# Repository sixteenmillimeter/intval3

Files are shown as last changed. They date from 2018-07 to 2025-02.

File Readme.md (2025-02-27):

# INTVAL3

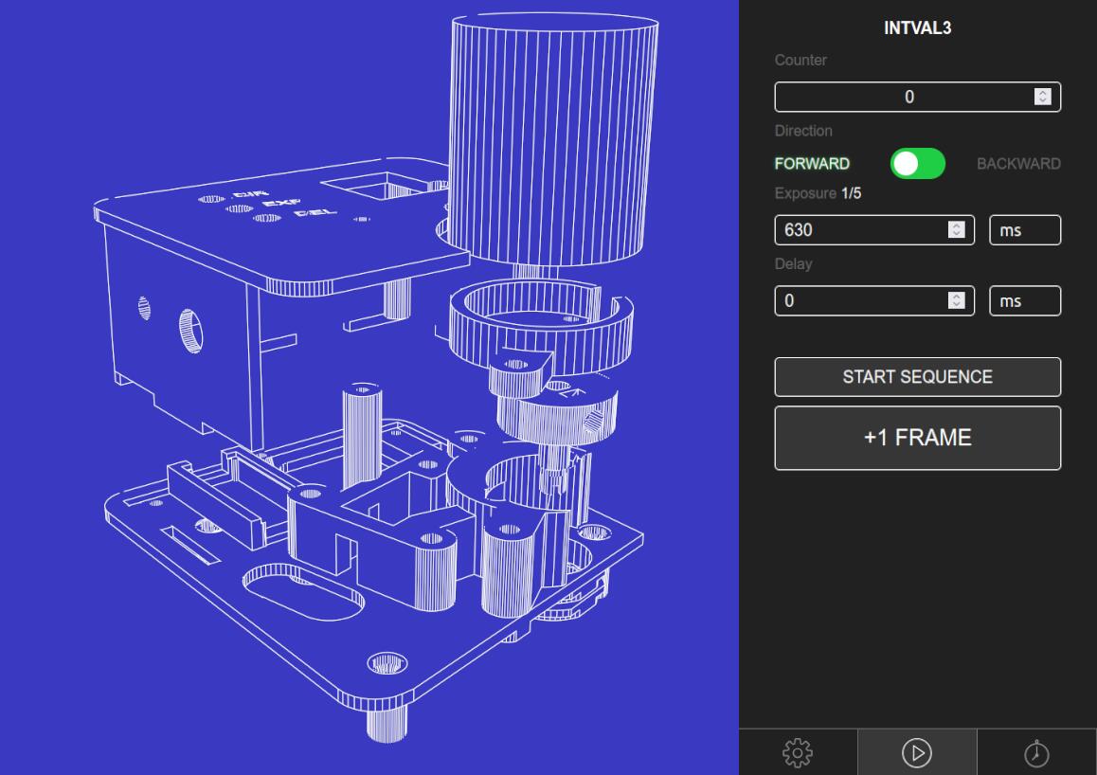
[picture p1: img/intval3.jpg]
intval3 wireframe rendering next to mobile app UI


### [Project Home - git.sixteenmillimeter.com/16mm/intval3](https://git.sixteenmillimeter.com/16mm/intval3)

* Github Mirror - [github.com/sixteenmillimeter/intval3](https://github.com/sixteenmillimeter/intval3)
* Gitlab Mirror - [gitlab.com/16mm/intval3](https://gitlab.com/16mm/intval3)

### What is this?

INTVAL3 is an open source intervalometer for the Bolex 16mm camera. The goal of the project is to create a cheap-to-make intervalometer that can be used to automate time-lapse or animation on the Bolex using mobile, web or physical controls.

This is the third incarnation of the INTVAL project, this time utilizing the [Raspberry Pi Zero W](https://www.raspberrypi.org/products/raspberry-pi-zero-w/) for Wifi and Bluetooth control. Earlier versions, the [INTVAL](https://github.com/sixteenmillimeter/INTVAL) and [INTVAL2](https://github.com/sixteenmillimeter/intval2) were Arduino-based. The original INTVAL used a solenoid (!!!) to hammer a camera release cable, while the second attempt was a proving ground for the motor-and-key hardware used in this version. 

The [INTVAL2](https://github.com/sixteenmillimeter/intval2) project should be used if you prefer a simpler, physical interface approach.

Does your browser support [Web Bluetooth](https://caniuse.com/#feat=web-bluetooth)? Control your INTVAL3 using this web app.

### [intval.sixteenmillimeter.com](https://intval.sixteenmillimeter.com)

### Components

* [Firmware](#firmware) for the Raspberry Pi Zero W running [Node.js](https://nodejs.org) on Raspian
* [Mobile app](#mobile) for controlling device using [Cordova](https://cordova.apache.org/) + [Bleno](https://github.com/sandeepmistry/bleno)
* [Web app](#web) for controlling device using [Restify](http://restify.com/)
* Hardware files, parts models for 3D printing, laser cutting and CNC
* PCB design for a Raspberry Pi Zero W Bonnet
* [Parts list](#parts-list)

## Firmware

The firmware of the INTVAL3 is a node.js application running on the Raspian OS intended for installation on the Raspberry Pi Zero W. 

## Mobile App

The INTVAL3 mobile app controls the intervalometer over Bluetooth. It can be used to configure the settings on the intervalometer such as exposure length, delay between frames and the direction of the film. The app can also be used to trigger individual frames, as well as start and stop sequences. As an experimental feature, film exposure settings can be determined with the camera on a mobile device.

## Web App

As a function of the firmware, there is an embedded web application that is hosted on the INTVAL3. When connected to a wifi network (via the mobile app) users are able to control the intervalometer from a browser. Users are also able to trigger functions and change settings on the intervalometer firmware from the command line by using cURL or wget, so actions can be scripted and automated from an external machine.

## Hardware

All of the non-electronic hardware is generated from OpenSCAD scripts and built into either STL files for 3D printing or DXF files for laser cutting or CNCing.

Electronics designs are available in the form of a Fritzing file, Gerber files, a wiring diagram and a mask image that can be used to fabricate a board from a blank PCB.

Prototype of the bare PCB of the "bonnet" for the Raspberry Pi Zero W are available for order from OSH Park. See the parts list below of components for this board.



<br />

## Parts

1. Raspberry Pi Zero W - [[Adafruit](https://www.adafruit.com/product/3400)] [[Sparkfun](https://www.sparkfun.com/products/14277)] [[Amazon](https://amzn.to/2Wf46J8)]
2. L298N Breakout Board - [[BC Robotics](https://www.bc-robotics.com/shop/l298n-motor-driver-board/)] [[Amazon](https://amzn.to/35CRFKa)]
3. 120RPM 12VDC Motor - [[Amazon](https://amzn.to/2YDGFe2)]
4. Microswitch w/ Roller - [[Adafruit](https://www.adafruit.com/product/819)] [[Amazon](https://amzn.to/2YDGFe2)]
5. L7805 5V Regulator - [[Adafruit](https://www.adafruit.com/product/2164)] [Sparkfun](https://www.sparkfun.com/products/107)] [[Amazon](https://amzn.to/2WaF39O)]
6. 2x Thru-hole Resistors - 330 Ohm
7. 1x Thru-hole Capacitor - 10 uF
8. 1x Thru-hole Capacitor - 100 uF
9. 4x Terminal blocks
10. 1x 3.5mm Socket Audio Connector - [[Amazon](https://amzn.to/2SGFVAY)]
11. 1x 3.5mm Stereo Audio Cable - [[Amazon](https://amzn.to/3beNPrQ)]
12. 1x Momentary Push Button 7mm Diameter - [[Amazon](https://amzn.to/2LavqBK)]
13. 1x Micro Switch w/ Roller Lever 28mm x 30.2mm x 10.2mm - [[Adafruit](https://www.adafruit.com/products/819)] [[Amazon](https://amzn.to/2SMBFzX)]
14. 1x Skateboard bearing 608-2RS - [[Amazon](https://amzn.to/3b7X2lC)]
15. 4x M3.5 - 0.6 x 20mm Screws
16. 3x M2 - 0.6 x 15mm Bolts
17. 6x M5 - 0.8 x 25mm Bolts
18. 4x M5 - 0.8 Nuts

* (Optional) Proto Bonnet - [[Adafruit](https://www.adafruit.com/product/3203)]
* (Optional) INTVAL3 Bonnet - [[OSH Park](https://oshpark.com/shared_projects/SkPyOK5S)]

## License
MIT License

Copyright (c) 2020 Matt McWilliams

Permission is hereby granted, free of charge, to any person obtaining a copy
of this software and associated documentation files (the "Software"), to deal
in the Software without restriction, including without limitation the rights
to use, copy, modify, merge, publish, distribute, sublicense, and/or sell
copies of the Software, and to permit persons to whom the Software is
furnished to do so, subject to the following conditions:

The above copyright notice and this permission notice shall be included in all
copies or substantial portions of the Software.

THE SOFTWARE IS PROVIDED "AS IS", WITHOUT WARRANTY OF ANY KIND, EXPRESS OR
IMPLIED, INCLUDING BUT NOT LIMITED TO THE WARRANTIES OF MERCHANTABILITY,
FITNESS FOR A PARTICULAR PURPOSE AND NONINFRINGEMENT. IN NO EVENT SHALL THE
AUTHORS OR COPYRIGHT HOLDERS BE LIABLE FOR ANY CLAIM, DAMAGES OR OTHER
LIABILITY, WHETHER IN AN ACTION OF CONTRACT, TORT OR OTHERWISE, ARISING FROM,
OUT OF OR IN CONNECTION WITH THE SOFTWARE OR THE USE OR OTHER DEALINGS IN THE
SOFTWARE.

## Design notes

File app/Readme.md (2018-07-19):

# INTVAL3

## Mobile App

The INTVAL3 mobile app is built using the Cordova framework for cross-platform deployment to iOS and Android.

## Requirements

* node.js
* npm
* Cordova
* XCode (for iOS) and/or
* Android Studio (for Android)

## Installation

All of the required plugins can be installed directly by executing the `install.sh` script on a system which supports bash. This script will use the `cordova` application to install the Cordova plugins. Cordova also supports the npm package.json format, so plugins may be alternately installed simply by running a `npm install` command from within the `app` directory.

## Building

Once all dependencies and plugins are installed, you can build the INTVAL3 app by running

```cordova build ios```

or

```cordova build android```

This generates the application source code in the `platforms` directory, under either the `ios` or `android` directory depending on your build target. The app can be built and run on your device by going to the project file and opening it in your IDE, either XCode or Android Studio. Alternately it can be run on your device using the `cordova run ios` or `cordova run android` commands.

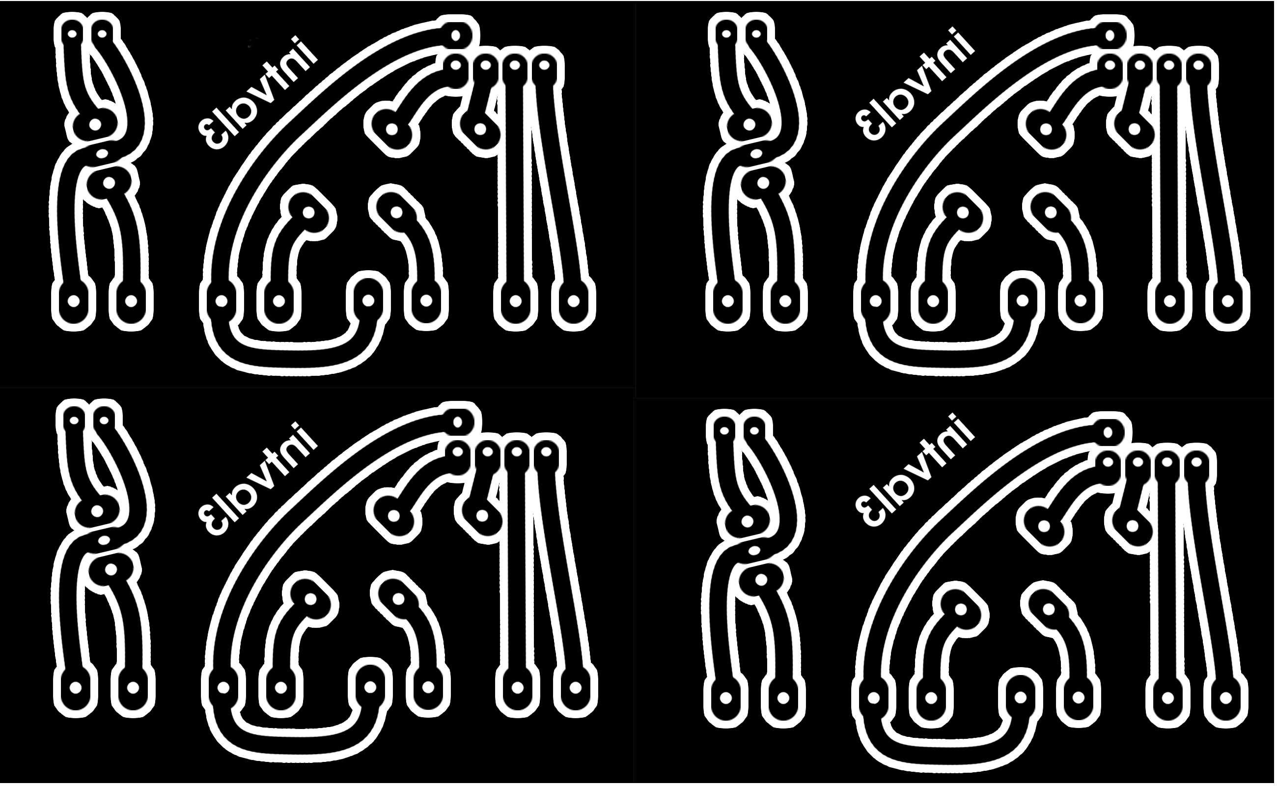
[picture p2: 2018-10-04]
hardware/intval3_0_prototype_mask_4_4x.png

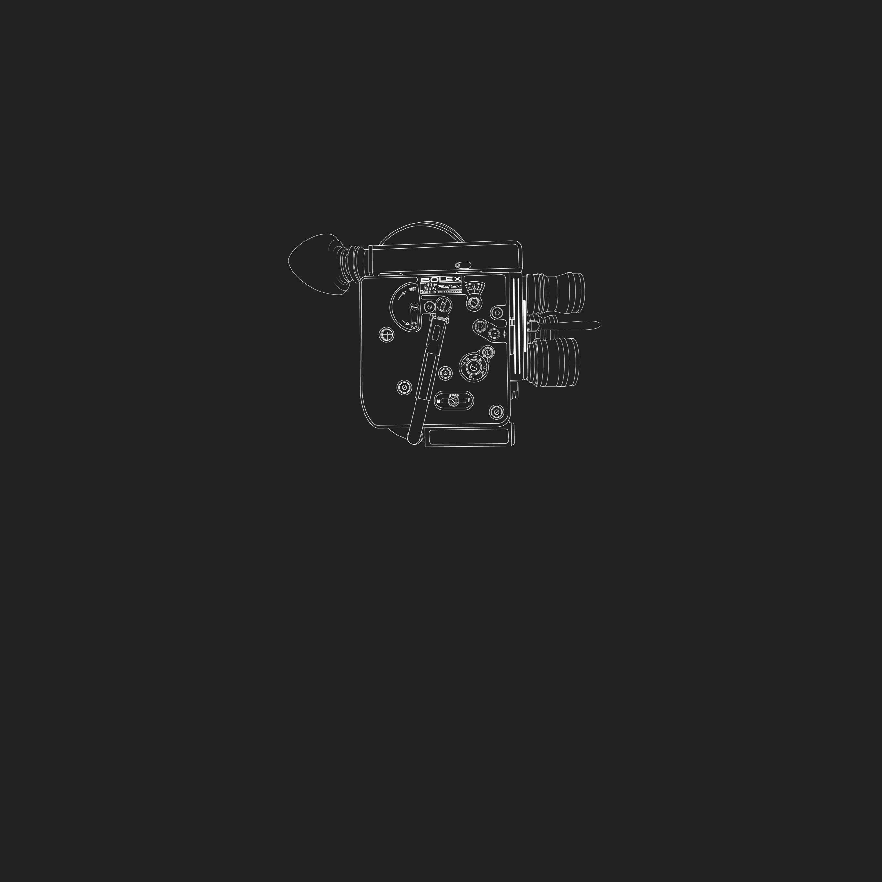
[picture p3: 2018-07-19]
app/res/screen/ios/Default@2x~universal~anyany.png

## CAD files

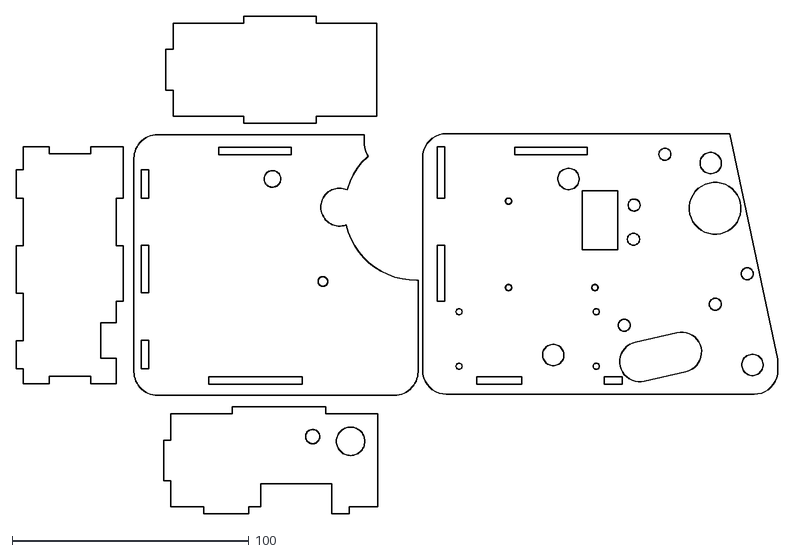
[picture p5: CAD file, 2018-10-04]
hardware/dxf/intval3_case.dxf
321.7 x 210.2

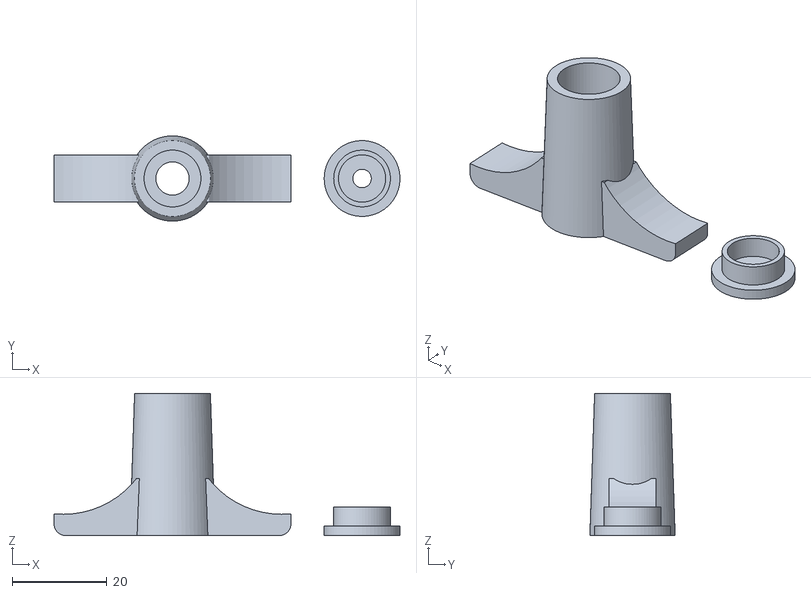
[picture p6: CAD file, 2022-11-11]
hardware/stl/intval3_plunger_plate.stl
73.0 x 18.0 x 30.0

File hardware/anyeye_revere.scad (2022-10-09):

module motor_set_screw_120 () {
    cube([10.19, 2.95, 2.95], center = true);
    translate([(10.19 / 2) - (2.56 / 2), 0, 0]) cube([2.56, 5.8, 5.8], center = true);    
}

module motor_set_screw_120_alt () {
    $fn = 60;
    cylinder(r = 2.95 / 2, h = 10.19, center= true);
    translate([0, 0, (10.19 / 2) - (2.56 / 2)]) cylinder(r = 5.8 / 2, h = 2.56, center = true);
}

module hobbled_rod_120 (h = 10) {
            d = 4.00;
        diff = 3.33;
    difference () {
        
        cylinder(r = d/2, h = h, center = true, $fn = 60);
        translate([d/2 + ((d/2) - (d - diff)), 0, 0]) cube([d, d, h + 1], center = true);
    }
}

module bearing_laser (x = 0, y = 0, z = 0, width= 8, hole = true) {
	innerD = 8.05;
	outerD = 22.1 - .4;
	fuzz = 0.1;
	translate ([x, y, z]) {
		difference () {
			cylinder(r = outerD / 2 + fuzz, h = width, center = true);
			if (hole) {
				cylinder(r = innerD / 2 - fuzz, h = width, center = true);
			}
		}
	}
}

/**
 *	Notched
 **/
module motor_key_120 (half = false, DECOYS = false, sides = 1, ALT = false) {
    
	outer_d = 27.5 + 2;
	notch_d = 10;
	height = 7 + 5 + 4;
	diff = 14 + 2.5 + 2;
    $fn = 60;
	difference () {
		union () {
			translate([0, 0, 12.1]) cylinder(r1 = 12 / 2, r2 = 12/2 + 4, h = 5, center = true);// padding against bearing
			translate([0, 0, diff + 1]) cylinder(r=outer_d/2, h= height -2, center= true, $fn=200); //large cylinder
			
		}
        //1 notch
		translate([0, 0, diff]) {
			translate ([-outer_d/2 - 2.5, 0, 0]) cylinder(r=notch_d/2, h= height, center= true); //notch
		}
		translate([0, 0, diff]) {
			translate ([-outer_d/2  -.5, -3.5 , 0]) rotate([0, 0, 100]) cube([15, 5, height], center = true); // smooth notch
			translate ([-outer_d/2  -.5, 3.5, 0]) rotate([0, 0, -100]) cube([15, 5, height], center = true); // smooth notch
		}
        
        if (sides == 2) {
            //2 notch
            translate([0, 0, diff]) {
                translate ([outer_d/2 + 2.5, 0, 0]) cylinder(r=notch_d/2, h= height, center= true); //notch
            }
            translate([0, 0, diff]) {
                translate ([outer_d/2  +.5, -3.5, 0]) rotate([0, 0, -100]) cube([15, 5, height], center = true); // smooth notch
                translate ([outer_d/2  +.5, 3.5, 0]) rotate([0, 0, 100]) cube([15, 5, height], center = true); // smooth notch
            }
        }
        
		//slot for hobbled(?) end
        translate([0, 0, 17 + 2]) {
             translate([0, 0, 6.5]) hobbled_rod_120(12);
            translate([6.42 - .2, 0, 4.3 - 1]) rotate([0, 90, 0]) motor_set_screw_120_alt();
            translate([14, 0, 4.3 - 1]) rotate([0, 90, 0]) cylinder(r2 = 6 / 2, r1 = 5.8 / 2, h = 6, center = true); //extension
            
        }
		//square void for bottom piece
		translate([0, 0, 10.5]) motor_key_bottom();
		
		if (half) {
			translate([0 - 50 , 0, -50]) cube([100, 100, 200]);
		}
	}
	
}

module motor_key_bottom () {
	$fn = 120;
	BEARING_INNER_D = 7.85;
	INNER_D = 4.08;
	OUTER_D = 11.08;
	FUZZ = 0.1;
	SQ = sqrt(pow(BEARING_INNER_D, 2) / 2);//largest square
	cube([SQ, SQ, SQ], center = true);
	translate([0, 0, -5.5]) cylinder(r=BEARING_INNER_D/2, h= 9, center= true);
	translate([0, 0, -5.5 - 5]) cylinder(r1= (INNER_D / 2) - FUZZ, r2= (INNER_D / 2) + FUZZ, h= 9.25, center= true);
	translate([0, 0, -5.5 - 4 - 1 - 1]) color(0, 0, 0) difference() {
		cylinder(r=(OUTER_D + 3) / 2, h = 6, center= true);
		translate([0, 0, -1.5]) cylinder(r2=(OUTER_D / 2) - FUZZ, r1=(OUTER_D / 2) + FUZZ, h = 6, center= true);
		translate([0, 0, .5]) rotate([90, 0, 0]) cylinder(r = 1, h = 20, center = true);
		translate([0, 0, -1.5]) cube([2, 20, 4], center = true);
	}
}

module reference_projector_shaft () {
	INNER_DIAMETER = 4.08;
	OUTER_DIAMETER = 11.08;
	H = 7.37;
	WHEEL_DIAMETER = 54;
	WHEEL_H = 3;
	STANDOFF = 6; 
	FUZZ = 0.1;
	
	$fn = 120;
	translate([0, 0, -15 + H]) difference () {
		cylinder(r = OUTER_DIAMETER / 2, h = 30, center = true);
		cylinder(r = INNER_DIAMETER / 2, h = 30 + 1, center = true);
	}
	translate([0, 0, -1.5]) cylinder(r = WHEEL_DIAMETER / 2, h = WHEEL_H, center = true); 
	translate([0, 0, H + 1.5 + STANDOFF]) difference () {
		cube([60, 60, 3], center = true);
		bearing_laser(hole=false);
	}
}

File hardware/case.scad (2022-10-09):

include <./modules.scad>
include <./variables.scad>

module l289N_holes (r = 3/2 - .2) {
    $fn = 60;
    DISTANCE = 36.5;
    H = 50;
    translate([0, 0, 0]) cylinder(r = r, h = H * 5, center = true);
    translate([DISTANCE, 0, 0]) cylinder(r = r, h = H * 5, center = true);
    translate([DISTANCE, DISTANCE, 0]) cylinder(r = r, h = H * 5, center = true);
    translate([0, DISTANCE, 0]) cylinder(r = r, h = H * 5, center = true);
}

module l289N_hole_test () {
    $fn = 40;
    difference () {
        cube([140, 40, 3], center = true);
        cylinder(r = 3/2, h = 50, center = true);
        translate([7, 0, 0]) cylinder(r = 3/2, h = 50, center = true);
        translate([7 * 2, 0, 0]) cylinder(r = 3/2 - .1, h = 50, center = true);
        translate([7 * 3, 0, 0]) cylinder(r = 3/2 - .2, h = 50, center = true);
        translate([7 * 4, 0, 0]) cylinder(r = 3/2 - .3, h = 50, center = true);
    }
}

module intval_panel_laser () {
    $fn = 40;
	difference () {
		union () {
			difference () {
				translate ([0, 0, 8.5]) {
					union () {
						translate([12 - 10, 0]) {
                            rotate([0, 0, -13]) {
                                rounded_cube([panel_2_x + 20 + 20, panel_2_y, 25.4/8], d = 20, center = true);
                            }
                        }
						//reinforces
						//translate([54, -12, -3]) rotate([0, 0, 89]) rounded_cube([110, 20, 4], 20, center = true);
						//translate([-17, 2, -3]) rotate([0, 0, 72]) rounded_cube([94, 13, 4], 13, center = true);
					}
				}
				for (i = [0 : len(xArray) - 1]) {
					bolex_pin_inner_laser(xArray[i], yArray[i]);
				}
			}
			//onetoone(26, 10, 4.5);
			//extends for onetoone
			

		}
		//onetoone(9, 14, 8.5);
		bearing_laser(54.5, 12, 6, width= 18, hole=false);
        translate([-38, -1, 0]) rotate([0, 0, -13]) l289N_holes();
        //translate ([6, -9, height + 3.5]) cylinder(r = bolt_inner, h = 50, center = true); //cover standoff hole
		//frame_counter_access(); //use the space
		m_p_access();
		remove_front();
		translate([6, 18, 0]) rotate([0, 0, -13]) cube([15, 25, 40], center=true); //motor wind key hole

		for (i = [0 : len(mm_x) - 1]) {
			translate([mm_x[i], mm_y[i], 0]) cylinder(r = bolt_inner, h = 100, center = true);
		}
        translate([0, 0, .25]) intval_laser_panel_cover();
            translate([-35, -24, 15]) rotate([0, 0, -13]) {
            translate([58 / 2, 23 / 2, 0]) cylinder(r = 3/2 - .2, h = 30, center = true, $fn = 20);
            translate([-58 / 2, 23 / 2, 0]) cylinder(r = 3/2 - .2, h = 30, center = true, $fn = 20);
            translate([58 / 2, -23 / 2, 0]) cylinder(r = 3/2 - .2, h = 30, center = true, $fn = 20);
            translate([-58 / 2, -23 / 2, 0]) cylinder(r = 3/2 - .2, h = 30, center = true, $fn = 20);
        }
	}

}

module intval_panel_laser_debug () {
    $fn = 40;
	difference () {
		union () {
			difference () {
				translate ([0, 0, 8.5]) {
					union () {
						translate([12 - 32.5, -5 + 9, 0]) {
                            rotate([0, 0, -13]) {
                                rounded_cube([panel_2_x + 20 + 65, panel_2_y, 25.4/8], d = 20, center = true);
                            }
                        }
						//reinforces
						//translate([54, -12, -3]) rotate([0, 0, 89]) rounded_cube([110, 20, 4], 20, center = true);
						//translate([-17, 2, -3]) rotate([0, 0, 72]) rounded_cube([94, 13, 4], 13, center = true);
					}
				}
				for (i = [0 : len(xArray) - 1]) {
					bolex_pin_inner_laser(xArray[i], yArray[i]);
				}
			}
			//onetoone(26, 10, 4.5);
			//extends for onetoone
			

		}
		//onetoone(9, 14, 8.5);
		bearing_laser(54.5, 12, 6, width= 18, hole=false);
        translate([-38, -1, 0]) rotate([0, 0, -13]) l289N_holes();
        //translate ([6, -9, height + 3.5]) cylinder(r = bolt_inner, h = 50, center = true); //cover standoff hole
		//frame_counter_access(); //use the space
		m_p_access();
		remove_front();
		translate([6, 18, 0]) rotate([0, 0, -13]) cube([15, 25, 40], center=true); //motor wind key hole

		for (i = [0 : len(mm_x) - 1]) {
			translate([mm_x[i], mm_y[i], 0]) cylinder(r = bolt_inner, h = 100, center = true);
		}
        intval_laser_panel_cover(DEBUG = true);
        translate ([4, 12, 0]) {
            translate([-51.5, -8.5, 0]) cylinder(r = 2.8/2, h = 100, center = true);
            translate([-51.5 - 66, -8.5 + 15, 0]) cylinder(r = 2.8/2, h = 100, center = true);
            translate([-51.5 + 11.5, -8 + 49, 0]) cylinder(r = 2.8/2, h = 100, center = true);
            translate([-51.5 - 54.5, -8.5 + 49 + 16, 0]) cylinder(r = 2.8/2, h = 100, center = true);
        }
	}
}

module bolex_pin_laser (x, y) {
	in = innerD;
    $fn = 120;
	translate ([x, y, 1]) {
		difference () {
			union () {
				translate([0, 0, (height / 2) - 3]) cylinder(r = (outerD + 5) / 2, h = 2, center = true);
				translate([0, 0, 1.175/2]) cylinder(r = outerD / 2, h = height + 1.175 , center = true);
			}
			cylinder(r = in / 2, h = height * 2, center = true);
			translate([0, 0, (height / 2) - 1.9]) cylinder(r1 =4.5 / 2, r2 = 6.7 / 2, h = 2, center = true);
            translate([0, 0, (height / 2) + 1]) cylinder(r = 6.7 / 2, h = 4, center = true);
		}
	}
}

module bolex_pin_laser_alt (x, y) {
    in = innerD;
    $fn = 120;
    translate ([x, y, 1]) {
        difference () {
            union () {
                translate([0, 0, (height / 2) + 1.5]) cylinder(r = (outerD + 1.5) / 2, h = 2, center = true);
                translate([0, 0, 1.175/2]) cylinder(r = outerD / 2, h = height + 1.175 - 1 , center = true);
            }
            cylinder(r = in / 2, h = height * 2, center = true);
            translate([0, 0, (height / 2) - 1.9]) cylinder(r1 =4.5 / 2, r2 = 6.7 / 2, h = 2, center = true);
            translate([0, 0, (height / 2) + 1]) cylinder(r = 6.7 / 2, h = 4, center = true);
        }
    }
}

module intval_laser_standoffs () {
    $fn = 40;
    for (i = [0 : len(xArray) - 1]) {
        bolex_pin_laser(xArray[i], yArray[i]);
	}
}

module intval_laser_standoffs_alt () {
    $fn = 40;
    for (i = [0 : len(xArray) - 1]) {
        bolex_pin_laser_alt(xArray[i], yArray[i]);
    }
}

module intval_laser_standoffs_plate () {
    $fn = 40;
    rotate ([0, 180, 0]) {
        bolex_pin_laser(0, 0);
        bolex_pin_laser(15, 0);
        bolex_pin_laser(0, 15);
        bolex_pin_laser(15, 15);
    }
    //decoys
    //translate([7, 7, 0]) decoys(23, 5.5, 6);
}

module intval_laser_standoffs_plate_alt () {
    $fn = 40;
    rotate ([0, 180, 0]) {
        bolex_pin_laser_alt(0, 0);
        bolex_pin_laser_alt(15, 0);
        bolex_pin_laser_alt(0, 15);
        bolex_pin_laser_alt(15, 15);
    }
    //decoys
    //translate([7, 7, 0]) decoys(23, 5.5, 6);
}

module bolex_pin_inner_laser (x, y) {
    $fn = 40;
    //innerD = 6.75;
    innerD = 9;
	translate ([x, y, 1]) {
		cylinder(r = innerD / 2, h = height * 2, center = true);
		//translate([0, 0, (height / 2) - 1]) cylinder(r1 =4.5 / 2, r2 = 6.5 / 2, h = 2, center = true);
	}
}

module bearing_laser (x, y, z, width= 8, hole = true) {
	innerD = 8.05;
	outerD = 22.1 - .4;
	fuzz = 0.1;
	translate ([x, y, z]) {
		difference () {
			cylinder(r = outerD / 2 + fuzz, h = width, center = true);
			if (hole) {
				cylinder(r = innerD / 2 - fuzz, h = width, center = true);
			}
		}
	}
}

module intval_laser_panel_cover (LASER = false, DEBUG = false, ALL_RED = false) {
    $fn = 60;
    cover_h = 16 + 3 + 4 + 10;
    MATERIAL = 25.4 / 8;

    module top () {
        difference () {
            rotate([0, 0, -13]) {
                translate([-10, 0, 0]) rounded_cube([120, panel_2_y, MATERIAL], d = 20, center = true);
            }
            translate([53, 12, 0]) cylinder(r = 30, h = 60, center = true); //hole for motor mount
            translate([22, 20, 0]) cylinder(r = 8, h = 60, center = true); // hole for moto mount bolt holder
            translate([53, 42, 0]) cylinder(r = 15, h = 60, center = true); //removes pointy part
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

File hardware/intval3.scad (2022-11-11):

include <./case.scad>
include <./mount.scad>
include <./plunger.scad>
//include <./anyeye_revere.scad>

/*

 INTVAL 3 

*/

module stl_plate () {
    //translate([0, 0, -0.5]) cube([150, 150, 1], center = true);
    translate([-60, 10, 7.5]) rotate([0, 180, 0]) intval_laser_standoffs_plate();
    translate([-27, 50, -9.5]) rotate([0, 0, 13]) translate([-40 + 2, -1, 14]) rotate([0, 0, -13]) l289N_mount();
    
    translate([23, 1, -5.75]) rotate([0, 0, 90]) motor_mount_bottom();
    translate([48, -13, 9]) rotate([0, 180, 0]) key_cap();
    translate([-5, -11, 3]) rotate([0, 0, 190]) geared_motor_mount_120();
    translate([65, 44, 26.5]) rotate([0, 180, 0]) motor_key_120();
    translate([15, -42, 15]) plunger_plate();
    translate([-52, -20, 85.5]) rotate([0, 180, -90]) motor_cap_120(false);
};

module dxf_plate () {
    translate([125, 0, 0]) rotate([0, 0, 13]) projection() intval_panel_laser();
    rotate([0, 0, 13]) intval_laser_panel_cover(LASER=true, ALL_RED=true);
};

module exploded_view () {
    intval_panel_laser();
    translate([0, 0, 5]) translate([-40 + 2, -1, 14]) rotate([0, 0, -13]) l289N_mount();
    translate([0, 0, 5]) motor_mount_bottom();
    translate([0, 0, 20]) motor_key_120();
    translate([one_to_one_x, one_to_one_y, 50]) geared_motor_mount_120();
    translate([one_to_one_x, one_to_one_y, 50]) motor_cap_120(false);
    //translate([0, 0, 60]) intval_laser_panel_cover(false, ALL_RED=true);
    translate([0, 0, -10]) intval_laser_standoffs_alt();
}

//exploded_view();
MODEL = "stl_plate";
if (MODEL == "stl_plate") {
    stl_plate();
} else if (MODEL == "plunger_plate") {
    plunger_plate();
} else if (MODEL == "standoffs_plate") {
    intval_laser_standoffs_plate();
} else if (MODEL == "standoff") {
    bolex_pin_laser(0, 0);
} else if (MODEL == "electronics_mount") {
    intval_electronics_mount();
} else if (MODEL == "motor_mount_bottom") {
    motor_mount_bottom();
} else if (MODEL == "motor_mount_120") {
    geared_motor_mount_120();
} else if (MODEL == "motor_key_120") {
    motor_key_120();
} else if (MODEL == "motor_key_120_reinforced") {
    motor_key_120_reinforced();
} else if (MODEL == "motor_key_120_reinforced_roller") {
    motor_key_120_reinforced_roller();
}

//rotate([0, 180, 0]) key_cap();

//plunger();
//plunger_top();
//motor_cap(false);
//rotate([0, 180, 0]) motor_cap_120(false);
//translate([0, 0, 39 / 2 + 5.75]) bolt_guide();
//intval_laser_standoffs_alt();
//intval_laser_standoffs_plate_alt();

LASER = "dxf_plate";
if (LASER == "laser_plate") {
    dxf_plate();
} else if (LASER == "panel") {
    intval_panel_laser();
} else if (LASER == "panel_cover") {
    intval_laser_panel_cover(true, ALL_RED=true);
}

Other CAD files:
hardware/modules.scad
hardware/mount.scad
hardware/plunger.scad
hardware/variables.scad

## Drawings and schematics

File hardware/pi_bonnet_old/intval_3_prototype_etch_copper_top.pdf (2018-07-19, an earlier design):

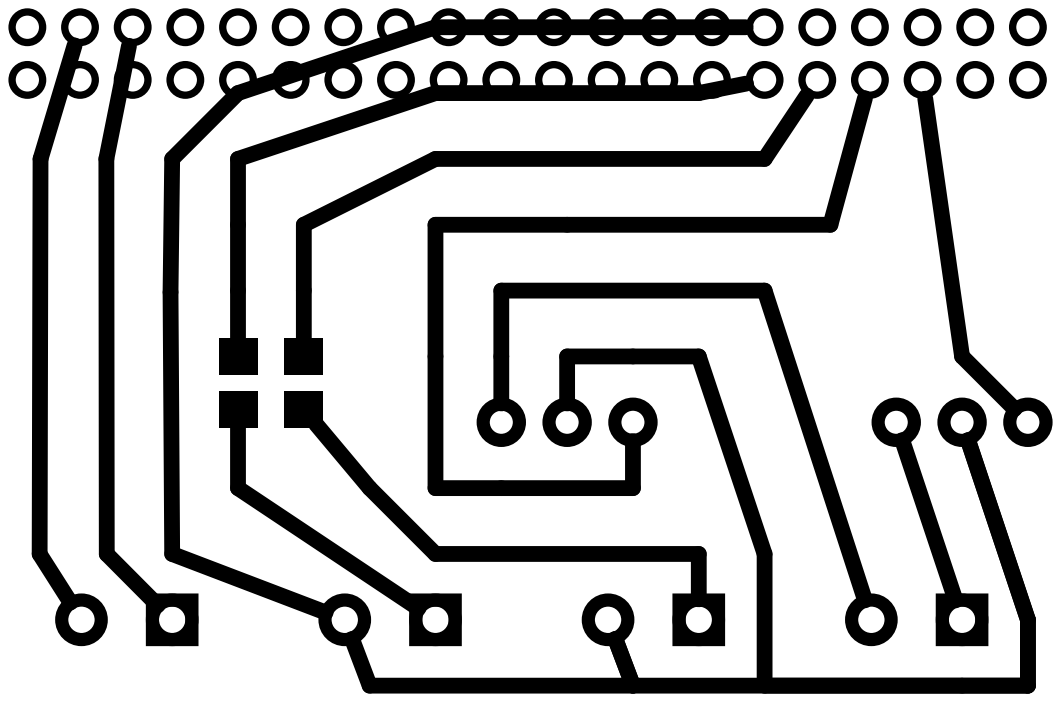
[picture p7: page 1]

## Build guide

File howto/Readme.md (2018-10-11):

## Assembly

The essential components of the intval3 intervalometer are the following parts:

The electronics that interface with the Raspberry Pi can be created in a few different ways. A board can be purchased (soon), put together by hand on a prototyping bonnet, or etched from copper-clad board using the circuit board design files.

## Installation

With a fresh [Raspian installation on the Raspberry Pi Zero W](RaspberryPiZeroW.md), you can install the intval3 software with two commands:

```
wget https://raw.githubusercontent.com/sixteenmillimeter/intval3/master/scripts/intval3-install.sh
sh ./intval3-install.sh

```

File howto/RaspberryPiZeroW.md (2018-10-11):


## Client Architecture

* Raspberry Pi Zero W
* Raspberry Pi Zero (Development)
* Raspberry Pi 1 (Development)

### Ethernet over USB

From [this blog post](http://blog.gbaman.info/?p=791)

1. Flash Raspbian Jessie full or Raspbian Jessie Lite onto the SD card.
2. Once Raspbian is flashed, open up the boot partition (in Windows Explorer, Finder etc) and add to the bottom of the ```config.txt``` file ```dtoverlay=dwc2``` on a new line, then save the file.
3. If using a recent release of Jessie (Dec 2016 onwards), then create a new file simply called ```ssh``` in the SD card as well. By default SSH is now disabled so this is required to enable it. Remember - Make sure your file doesn't have an extension (like .txt etc)!
4. Finally, open up the ```cmdline.txt```. Be careful with this file, it is very picky with its formatting! Each parameter is seperated by a single space (it does not use newlines). Insert ```modules-load=dwc2,g_ether``` after ```rootwait```. To compare, an edited version of the ```cmdline.txt``` file at the time of writing, can be found here.
5. That's it, eject the SD card from your computer, put it in your Raspberry Pi Zero and connect it via USB to your computer. It will take up to 90s to boot up (shorter on subsequent boots). It should then appear as a USB Ethernet device. You can SSH into it using  raspberrypi.local as the address.

### Sharing internet from host machine (OSX)

From [learn.adafruit.com](https://learn.adafruit.com/turning-your-raspberry-pi-zero-into-a-usb-gadget?view=all)

```sudo nano /etc/network/interfaces```

Enable wlan0 by adding the following lines:

```
allow-hotplug wlan0
iface wlan0 inet manual
	wpa-conf /etc/wpa_supplicant/wpa_supplicant.conf
```

Enable with ```sudo systemctl enable wpa_supplicant.service```.

For usb connection, add at the end:

```
allow-hotplug usb0
iface usb0 inet static
        address 192.168.7.2
        netmask 255.255.255.0
        network 192.168.7.0
        broadcast 192.168.7.255
        gateway 192.168.7.1
```

This will give the Raspberry Pi the IP Address ```192.168.7.2```. Then run the following:

```
sudo ifdown usb0
sudo ifup usb0
ifconfig usb0
```

In the OSX Network Preferences you'll see the device show up as an ```RNDIS/Ethernet Gadget```. It'll probably be set up for DHCP by default so change it to ```Configure IP4 Manually```. Use the following settings:

```
IP address: 192.168.7.1
Subnet Mask: 255.255.255.0
Router: 192.168.7.1
```

Apply changes. Next, enable internet sharing from your machine (Ethernet or Wifi) to the ```CDC``` or ```RNDIS``` Raspberry Pi.

On the Pi, change the line in ```/etc/network/interfaces``` that reads ```auto lo``` to ```auto lo usb0```. Remove or comment out the lines added to the file below ```allow-hotplug usb0``` previously and replace with ```iface usb0 inet manual```.

### Modules and guides
* [BLE and pi and mobile app](https://www.hackster.io/inmyorbit/build-a-mobile-app-that-connects-to-your-rpi-3-using-ble-7a7c2c)
* [pi and i2c](http://www.maxbotix.com/Setup-Raspberry-Pi-Zero-for-i2c-Sensor-151/)
* [gpio module](https://www.npmjs.com/package/rpi-gpio)

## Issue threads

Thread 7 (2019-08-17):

In web bluetooth mode, set wifi button is broken

sixteenmillimeter, 2019-08-17:

sixteenmillimeter, 2019-10-31:
Wifi passwords are not being properly escaped

sixteenmillimeter, 2020-05-16:
pwa code seems to be calling out to ble code. Track down why "mobile" object is being referenced where "pwa" should be used.

Closed 2020-05-16.

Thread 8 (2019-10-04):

iOS app throws an error on startup, even when successfully connected to device

sixteenmillimeter, 2019-10-04:
Error message is "Could not find peripheral UUID (null)". Investigate and resolve this error.

sixteenmillimeter, 2020-01-02:
Resolved with last commit.

Closed 2020-01-02.

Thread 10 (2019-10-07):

Sometimes frames are doubled

sixteenmillimeter, 2019-10-07:
Happening during sequences. Very likely mechanical problem. Maybe there is a software fix to shut off after x milliseconds if microswitch doesn't engage. Or stop?

Closed 2019-10-31.

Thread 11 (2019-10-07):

Start/Stop sequence UI is buggy

sixteenmillimeter, 2019-10-07:
Sequences starting and stopping on iOS UI inconsistently. UI isn't responsive enough and it's leading to double starts (is that possible).

sixteenmillimeter, 2019-10-31:
Sequence has been re-written to prevent multiple sequences or multiple frames

Closed 2019-10-31.

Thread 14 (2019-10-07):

Add ability to shoot specified number of frames

sixteenmillimeter, 2019-10-07:
Shoot  `n` frames in a sequence and then stop.

sixteenmillimeter, 2019-10-31:
Resolved and attached to web and ble endpoints

Closed 2019-10-31.

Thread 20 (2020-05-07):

iOS app prevents single frame button from working after running sequence

sixteenmillimeter, 2020-05-07:
Need to reproduce exact issue, but either the single frame button or entire UI freezes up after running a sequence. This could be a flag not being reset after sequence is complete, or an uncaught exception.

sixteenmillimeter, 2020-05-15:
Located flag but have not fixed issue. Will test in web app first, as I have a macOS/Xcode/iOS mismatch at the moment.

sixteenmillimeter, 2020-05-16:
Resolved in commit 2dc24ce

Closed 2020-05-16.

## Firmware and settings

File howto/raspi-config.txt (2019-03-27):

/* Command strings */
#define GET_CAN_EXPAND  "sudo raspi-config nonint get_can_expand"
#define EXPAND_FS       "sudo raspi-config nonint do_expand_rootfs"
#define GET_HOSTNAME    "sudo raspi-config nonint get_hostname"
#define SET_HOSTNAME    "sudo raspi-config nonint do_hostname %s"
#define GET_BOOT_CLI    "sudo raspi-config nonint get_boot_cli"
#define GET_AUTOLOGIN   "sudo raspi-config nonint get_autologin"
#define SET_BOOT_CLI    "sudo raspi-config nonint do_boot_behaviour B1"
#define SET_BOOT_CLIA   "sudo raspi-config nonint do_boot_behaviour B2"
#define SET_BOOT_GUI    "sudo raspi-config nonint do_boot_behaviour B3"
#define SET_BOOT_GUIA   "sudo raspi-config nonint do_boot_behaviour B4"
#define GET_BOOT_WAIT   "sudo raspi-config nonint get_boot_wait"
#define SET_BOOT_WAIT   "sudo raspi-config nonint do_boot_wait %d"
#define GET_SPLASH      "sudo raspi-config nonint get_boot_splash"
#define SET_SPLASH      "sudo raspi-config nonint do_boot_splash %d"
#define GET_OVERSCAN    "sudo raspi-config nonint get_overscan"
#define SET_OVERSCAN    "sudo raspi-config nonint do_overscan %d"
#define GET_CAMERA      "sudo raspi-config nonint get_camera"
#define SET_CAMERA      "sudo raspi-config nonint do_camera %d"
#define GET_SSH         "sudo raspi-config nonint get_ssh"
#define SET_SSH         "sudo raspi-config nonint do_ssh %d"
#define GET_VNC         "sudo raspi-config nonint get_vnc"
#define SET_VNC         "sudo raspi-config nonint do_vnc %d"
#define GET_SPI         "sudo raspi-config nonint get_spi"
#define SET_SPI         "sudo raspi-config nonint do_spi %d"
#define GET_I2C         "sudo raspi-config nonint get_i2c"
#define SET_I2C         "sudo raspi-config nonint do_i2c %d"
#define GET_SERIAL      "sudo raspi-config nonint get_serial"
#define GET_SERIALHW    "sudo raspi-config nonint get_serial_hw"
#define SET_SERIAL      "sudo raspi-config nonint do_serial %d"
#define GET_1WIRE       "sudo raspi-config nonint get_onewire"
#define SET_1WIRE       "sudo raspi-config nonint do_onewire %d"
#define GET_RGPIO       "sudo raspi-config nonint get_rgpio"
#define SET_RGPIO       "sudo raspi-config nonint do_rgpio %d"
#define GET_PI_TYPE     "sudo raspi-config nonint get_pi_type"
#define GET_OVERCLOCK   "sudo raspi-config nonint get_config_var arm_freq /boot/config.txt"
#define SET_OVERCLOCK   "sudo raspi-config nonint do_overclock %s"
#define GET_GPU_MEM     "sudo raspi-config nonint get_config_var gpu_mem /boot/config.txt"
#define GET_GPU_MEM_256 "sudo raspi-config nonint get_config_var gpu_mem_256 /boot/config.txt"
#define GET_GPU_MEM_512 "sudo raspi-config nonint get_config_var gpu_mem_512 /boot/config.txt"
#define GET_GPU_MEM_1K  "sudo raspi-config nonint get_config_var gpu_mem_1024 /boot/config.txt"
#define SET_GPU_MEM     "sudo raspi-config nonint do_memory_split %d"
#define GET_HDMI_GROUP  "sudo raspi-config nonint get_config_var hdmi_group /boot/config.txt"
#define GET_HDMI_MODE   "sudo raspi-config nonint get_config_var hdmi_mode /boot/config.txt"
#define SET_HDMI_GP_MOD "sudo raspi-config nonint do_resolution %d %d"
#define GET_WIFI_CTRY   "sudo raspi-config nonint get_wifi_country"
#define SET_WIFI_CTRY   "sudo raspi-config nonint do_wifi_country %s"
#define CHANGE_PASSWD   "(echo \"%s\" ; echo \"%s\" ; echo \"%s\") | passwd"

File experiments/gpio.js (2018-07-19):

'use strict'

const Gpio = require('onoff').Gpio

let release
let micro
let fwd
let bwd

process.on('SIGINT', () => {
	if (fwd && fwd.writeSync) {
		console.log(`Setting fwd to 0`)
		fwd.writeSync(0)
	}
	if (bwd && bwd.writeSync) {
		console.log(`Setting bwd to 0`)
		bwd.writeSync(0)
	}
	process.exit()
})

function releaseTest () {
	const PIN = 6
	release = Gpio(PIN, 'in', 'both')
	console.log(`Watching input on GPIO 0${PIN}`)
	let saveTime = 0
	let active = false
	release.watch((err, val) => {
		const NOW = +new Date()
		/* Button + 10K ohm resistor */
		/* 1 = open */
		/* 0 = closed */
		if (err) {
			return console.error(err)
		}
		//console.log(`Release switch val: ${val}`)
		//console.log(`RELEASE: ${val} ${active} ${NOW} ${saveTime}`)
		if (val === 0) {
			//console.log('closed')
		} else if (val === 1) {
			//console.log('open')
		}
		if (val === 0) {
			//closed
			if ((!active && saveTime === 0) || (active && NOW - saveTime > 10 * 1000)) {
				saveTime = NOW
				active = true //maybe unncecessary 
			} else {
				//saveTime = 0
				//active = false
			}
		} else if (val === 1) {
			//open
			if (active) {
				if (NOW - saveTime > 50 && NOW - saveTime < 1000) {
					console.log('Started Frame')
				} else if (NOW - saveTime >= 1000) {
					console.log('Started Sequence')
				}
				//console.log(`Release closed for ${NOW - saveTime}`)
				saveTime = 0
				active = false
			}
		}
	})
}

function microTest () {
	const PIN = 5
	micro = Gpio(PIN, 'in', 'both')
	console.log(`Watching input on GPIO 0${PIN}`)
	let saveTime = 0
	let frameActive = true //this._state.frame.active
	let primed = false //this._state.primed
	micro.watch((err, val) => {
		const NOW = +new Date()
		if (err) {
			return console.error(err)
		}
		console.log(`Micro switch val: ${val}`)
		if (val === 0) {
			//console.log('closed')
		} else if (val === 1) {
			//console.log('open')
		}
		if (val === 0 && frameActive) {
			if (!primed) {
				primed = true
				saveTime = NOW
				console.log('Primed')
			}
		} else if (val === 1 && frameActive) {
			if (primed) {
				primed = false
				setTimeout( () => {
					console.log(`Stop Frame after ${NOW - saveTime}`)
				}, 10)
			}
		}
	})
}

//test stepping up of 3.3V RPI logic via 
//Sparkfun PRT-10968 (NPC1402)
function stepupTest () {
	const FWD = 13 // RPIO PIN 13
	const BWD = 19
	fwd = Gpio(FWD, 'out')
	bwd = Gpio(BWD, 'out')

	console.log(`Setting pin ${BWD} high`)
	fwd.writeSync(0)
	bwd.writeSync(1)
}

releaseTest()
microTest()
//stepupTest()

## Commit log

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2017-09-16 Watch not responding to shorts, use set interval with a readSync()
    [gpio.js]
2017-09-16 GPIO 05 works with pulldown resistor
    Now try with built in watch command
2017-09-17 Updated default behavior of frame
    Also added a parallel example of the logic to gpio.js
2017-09-17 Caught major oversight. 1 = open
    Therefore frame event needs to be determined on open, after started
    when closed
2017-09-17 Fixed over 1000ms sequence logic
    [gpio.js]
2017-09-18 Remove extra log events
    Test running test for extended length of time to test whether or not
    errant 0 change events trigger frames
2017-09-18 More complex logic to prevent errant closed events from breaking
    [gpio.js]
2017-09-19 Use PINS configuration object to initialize pins
    TODO: Separate into file, automatically switching out for different
    models
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2017-09-23 Still reading 1.6V on GPIO pin set high
    Possibly damaged pin 18
    [gpio.js]
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2017-09-25 Intval 3 board prototype
    Design roughed in fritzing, the pdf pulled into photoshop and hand
    routed.
    [intval_3_prototype.fzz]
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2017-10-20 Release pin is crashing lib
2017-10-20 Refactor releaseWatch to use a seperate function to determine close state for the release switch
2017-10-20 Test frame (and see why release switch is causing a hard exit)
2017-10-20 Stop resetting frame.start to 0
2017-10-20 Remove voltage step-up chips and add a voltage regulator for regulating 5v from a 12v source
    [intval_3_prototype.fzz]
2017-10-20 If statements were eating the frame continuance step. This has been altered by using 0 as the default value for arbitrary exposure frames.
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2017-10-21 Harden the logic which allows exposures at arbitrary exposure times. A "pause" variable has been added to the frame state that tracks when the frame is intentionally paused, preventing the premature 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
2017-10-21 Set pause flag before frame is actually paused. To prevent stop events when motor slows.
2017-10-21 Reduce "closed" time by 50ms. Is still too long when frame fires. Logging might be the culprit
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2017-10-21 Ok backwards frames are apparently doing fine. This commit uses a better organized object structure for release variables.
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2017-10-21 Force example frame before evaluating query and body of post for parameters
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2017-10-21 Add logic to prevent frames shorter than 250ms. Might work for now. Seemingly only happening with web requests?
2017-10-22 All features added to /frame endpoint, can set direction independent of the state and can set the exposure as well.
2017-10-22 Start UI, add jquery and a switch for web and mobile methods
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2017-10-22 Get state at startup (to maintain state on the device and report to the client on reload). Also, settings UI in place, need mscript UI as well.
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2017-10-23 Persist device state with node-persist. This allows multiple controllers to share state, and for device to maintain settings between shutdowns.
2017-10-23 Added /reset endpoint to reset device state.
2017-10-24 Begin re-write of intval hardware files.
    [case.scad, intval3.scad, modules.scad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]
2017-10-24 Start adapting case to new size requirements.
    [case.scad, intval3.scad]
2017-10-25 Position tabs on case side pieces using arguments, not hardcoded values.
    [case.scad]
2017-10-25 Test case ready to cut
    [case.scad, intval3.scad]
2017-10-25 Made minor adjustments to case for better fit and for access.
    [case.scad]
2017-10-27 electronics_mount doesnt exist, just use l289N_mount
    [intval3.scad]
2017-10-27 Use local stash
    [intval3.scad]
2017-10-27 Extend the panel attachment tube to reach the top of the panel
    [mount.scad]
2017-10-27 Adjust length of panel connection
    [intval3.scad, mount.scad]
2017-10-27 Tighten up board design
    [intval_3_prototype.fzz]
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2017-11-03 Update PCB design to use raspberry pi 3 headers. Use 5mm terminal blocks.
    [intval_3_prototype.fzz]
2017-11-08 V4 prototype of the board. This one goes to production.
    [intval_3_prototype.fzz]
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2017-11-20 Update to larger dc jack for intval case.
    [case.scad, intval3.scad]
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2017-11-21 Remove post body from frame, reverse frames are not happening.
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2017-11-22 Motor cap to print.
    [intval3.scad]
2017-11-22 Attach functions to the window option so that cordova does not break.
2017-11-23 Add sqlite3 and table logging functionality. Track all frames all the time.
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2017-11-28 Enlarge the panel mount column
    [intval3.scad, mount.scad]
2017-12-07 Key_cap sizing improved
    [case.scad, intval3.scad]
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2017-12-15 Begin designing a carriage and stand for the intval.
    [carriage.scad]
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2017-12-21 use the microdelay to prevent multiple frames
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2017-12-21 Start and stop worked in web lib, but GUI didn't. This is a fix that shuts off the "sequence" button when sequence is stopped.
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2017-12-30 Fix intval button text changes
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2017-12-30 Carriage belonged to the mcopy project, was misplaced here
    [carriage.scad]
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2018-01-09 Prevent motor from stopping before 100ms. Took out the logging in watchMicro, due to the fact that the problem with backwards frames was likely a bad connection.
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2018-02-03 Camera exposure logic is in place. Will take a photo with the device camera and use the exif data to determine the correct exposure for the bolex.
    - Determines # of stops between fstop of phone and set fstop of bolex
    - Determines # of stops between iso of phone and set iso of bolex
    - Compensates for the 0.8 prism constant
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2018-02-08 Add a reset feature to mobile app which allows the device to be reset to the default settings (direction forward, exposure 630 and delay 0).
2018-02-10 Moved loosely defined tests and tinkering scripts to a directory called "experiments"
    [gpio.js]
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2018-08-09 Intval case dxf for cutting
    [intval3_case.dxf]
2018-08-09 Start reinfoced key
    [mount.scad]
2018-08-16 Electronics work
    [intval3.scad]
2018-08-17 MAster mold for 120 key, test molds
    [mount.scad]
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2018-10-04 Add an STL plate of all printable items
    [intval3.scad]
2018-10-04 Move dxf files into their own directory
    [intval3_case.dxf]
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2018-10-09 Tweak intval key for new bearings
    [case.scad, intval3.scad]
2018-11-10 Add a bolt guide
    [case.scad]
2019-02-22 Update board size
    [intval_3_prototype.fzz]
2019-03-08 Export raspberry pi zero w bonnet as gerber files and make a .zip of them to upload to OSHPark. Boards will be released as gerber files and pdf for etching your own boards manually, using the toner t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
    [intval_3_prototype.fzz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]
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2019-03-26 Work on anyeye revere projector.
    [anyeye_revere.scad]
2019-03-27 Add list of raspi-config commands
    [raspi-config.txt]
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2019-10-31 Prevent frame from running if _state.frame.active is true.
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2020-05-16 Caught issue where frame function doesn't work after sequence is run.
2020-05-16 PWA wifi functions were not attached to DOM elements, only mobile ones. getWifi, setWifi and editWifi bindings were added to both pwa.init and mobile.init functions and DOM elements were bound to the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
2020-07-09 Motor key is now printable without supports inside the set screw void and the hobbled rod void.
    [intval3.scad, mount.scad]
2020-07-25 Failed to install with lts, switched back to 9.9.0
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2021-03-28 New standoffs design
    [case.scad]
2021-03-28 Use new standoffs design in exploded view
    [intval3.scad]
2021-05-02 Add reinforced motor key design with a notched corner
    [intval3.scad, mount.scad]
2022-10-09 Work in progress of adding Makefile to build all OpenSCAD models for printing. Based off work in intval2 project with a slightly more automated approach. Hopefully can massage the parseVars.sh script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
    [anyeye_revere.scad, case.scad, intval3.scad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]
2022-11-11 Add the reinforced key design from intval2
    [intval3.scad, intval3_plunger_plate.stl]
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
